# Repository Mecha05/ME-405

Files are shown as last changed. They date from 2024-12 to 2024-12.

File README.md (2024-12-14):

# ME-405
ME-405 Romi Portfolio

## Required materials:
1) Romi chasis of your desired color
2) Romi Drive and caster wheels
3) BNO055 IMU Breakout Board
4) Modified shoe of Brian
5) Nucleo L476RG
6) M2.5 x 8mm Standoff
7) M2.5 x 10mm Standoff
8) M2.5 x 30mm Standoff
9) M2.5 x 6mm Socket Head Cap Screw
10) M2.5 x 8mm Socket Head Cap Screw
11) M2.5 x 10mm Socket Head Cap Screw
12) M2.5 Nylon Lock Nuts
13) M2.5 Nylon Washers
14) Custom Romi to shoe adapter
15) Gearmotor and Encoder assembly
17) Motor driver and PDP for Romi
18) 8-channel QTRX sensor array
19) Bumper Switch Assembley (Right, Left, or both)
20) Assorted tools
21) Attached .txt files
22) Female to Felmale wires
23) Optional HC-05 Bluetooth modules

## **Getting Started:**
To get started follow the set-up instructions provided with the Romi chassis and on the Romi webpage to secure and attach the Motor driver and PDP for Romi, Gearmotor and Encoder assembly, and Romi Drive and caster wheels. The Gearmotor and Encoder assembly should plug directly into the PDP.

Romi should now look like this:


These highlighted section show necessary cable connections for power to the Nucleo, Motor control cables, and Encoder cables for communication between the PDP and our Nucleo. Example cables are shown below.



Following this step please attach the BNO055 IMU Breakout Board, in the specified location shown below. A different location may be needed depending on the quantity and location of bump sensors. Consider a custom mount on the aft part of Romi as the best solution.



Next step in to wire up the IMU, the necessary pins are power, ground, SDA, SCL, and RST. An example Cable set up is provided below:


Wiring the 8-channel QTRX sensor array comes next, I reccomend creating your cables using a 7x1 joined female end to 7 free ends to enable a solid connection on the array board while giving freedom to use any desired pins on the Nucleo. A pin our of the array board are given below.


To install the 8-channel QTRX sensor array, first fish the wire through the highlighted holes on the bottome of the Romi, shown belown, then place the board in the left over gap. You will need to secure the board, however be aware of blocking sensors or potential shorts. I reccomend taping the 7x1 joined adaptor to the standoffs for the nucleo, but do what every feels most secure.



This is what the bottom of Romi should look like after the instalation.


The final step in Romi assebly before wiring is the bump sensors. You are welcome to choose as many or as few as you would like. For our project we chose the Right assembly only. This was doen to avoid having to relocate the IMU. You will need a 4x1 cable and I reccomend having one end of this cable be 1x1s for port avalibility. The attached system should look like this (note this is with both installed)



## Wiring Set-Up:
Next step is the most critical to ensure that Romi opperates as intended. Below is the wiring diagram that we used for our project. If different ports are needed please reflect those changes in the code to ensure proper function.



> [!WARNING]
> Make sure to verify all ports, esspecially ground and power, before turning the system on. If not possible damage could occur to the components or sensors.

## Code Set-Up:
After verifying that your physcial pins match those specified in the code, load all of the attached .txt files into your python 3 program of choosing and save the file to the Romi as a .py file. Make sure that the .py file names match those verbatum of those of the .txt files, otherwise erros may occur.

The overall structure of the code to run the Romi around the track involves three states: Left Wheel, Right Wheel, and Velocity Control. The Left Wheel tasks runs the left motor and encoder of the Romi and controls the duty cycle based on a reference velocity specified from the velocity control task and a measured velocity from the left encoder. The Right Wheel tasks similarly runs the right motor and encoder of the Romi, controlling the duty cycle based on the reference velocity and the measured velocity from the left encoder. The Velocity control taks is the larger task, which controlls the overall behavior of the Romi. The velocity control task reads reads the line sensor data, calculates a weighted sum, and specifies a yaw rate based on the value of the weighted sum. Our control structure is a cascaded control structure with the left and right wheel motor controllers on the inner loop in the Left Wheel and Right Wheel tasks. The outer loop of our control system is contained within the velocity control task and it involves a longitudinal velocity controller and a yaw rate controller, which feed reference wheel velocities to the other two controllers. All the shares variables, motor objects, and controller must be defined correctly within all of the states to ensure good communication. Thec scheduler included in the cotask and task_share runs the tasks on time at a period of 6 miliseconds for the Left and Right Wheel Encoders and 8 ms for the velocity control task.

## Task Diagram

Term Project Task Diagram

The task diagram shows the interaction between the three different tasks. The task diagram shows that the left and right wheel tasks have a higher priority and shorter period than the velocity control task. The left and right wheel reference velocities are shared from the velocity control task, while the measured left and right wheel measured velocities are shared from the left and right wheel tasks respectively to the velocity control task. These velocities allow the controllers for each motor to control the motor speed to match the reference velocity calculated from the yaw rate and linear velocity controllers in the velocity task. Additionally, these share variables allow the yaw rate and linear velocity tasks to update based on the measured velocity from the left and right wheel tasks. The calibration flag, bump flag, and end flag variables are shared from the velocity control task to signal when the IMU has calibrated on startup, when the bump sensors are triggered, and when the Romi has reached the end of the track.

## Left Wheel Task

Left Wheel FSM

The Left Wheel Task Finite State Machine displays the three states within the Left Wheel task. State 0 is simply a setup state that runs only until the calibration flag reads true once the IMU has been calibrated in the Velocity Control task. State 1 is the state where the control of the motor occurs. State 1 updates the left encoder and calculates the measured velocity of the left wheel. State 1 takes in the shares variable, including the reference velocity of the left wheel from the Velocity Control task, which is fed into the left wheel PI controller. The left wheel controller will return a duty cycle for the motor to keep the measured velocity of the wheel at the reference velocity. Finally, state 1 also puts the velocity of the left wheel into the shares variable to be used in the Velocity Control task. State 2 is used to avoid the wall and return to the start once the bump flag or end flag is true, which has been harcoded within the Velocity Control task, meaning the left wheel task is in an idle state until the bump flag and end flag are false.

## Right Wheel Task

Right Wheel FSM

Similar to the Left Wheel Task, the Right Wheel Task Finite State Macine shows the three states within the Right Wheel task. State 0 runs and sets up the motor until the calibration flag reads true after the IMU has been calibrated in the Velocity Control Task. State 1 controls the right motor by updating the right aencoder and calculates the measured velocity. It also takes in the reference velocity of the right wheel from the Velocity control task, which is used in the right wheel PI controller. The PI controller returns a duty cycle to update the motor and keep the measured velocity of the right wheel at the reference velocity. State 2 is used to avoid the wall and return to the start once the bump flag or end flag is true, which has been haroded within the Velocity Control task, measning the left wheel task is in an idle state until the bump flag and end flag are flase.

## Velocity Control Task

Velocity Control FSM

The Velocity Control Task Finite State Machine shows the 4 states that are within the Velocity Control task. State 0 is a velocity setup task that initlizes the important objects, such as the line sensors, and calirates the IMU. Once the IMU is calibrated, the task will transition to state 1 and it will signal to the Left and Right Wheel Tasks that they must transition to state 1 as well. State 1 is where the majority of the control stucture is taking place. The state reads each of the line sensors, normalizes the reading, and calculates the weighted sum of the line sensor readings. Based on the value of the weighted sum, we update the yaw rate to control the behavior of the motor. If the absolute value of the weighted sum is small drive the motor straight when it is reading equal amounts of black and white on each side of the line sensor array. If the absolute value of the weighted sum is very large, the linear velocity of the Romi robot is decreased for the sharp curves to increase accuracy of reading the tight radii. If it has been less than about 2 seconds since the last sharp turn reading from the line sensor array, the Romi will continue to go slow. To ensure that the initial line of the starting box does not affect the robot, a condition has been included that will cause the Romi to continue straight if it reads 3 or more of the sensors over a black line in about 5 seconds after the Romi starts moving. The same logic is implemented to ignore when 5 or more of the sensors read as all black so that the Romi continues along the course track even with large vertical black lines in the path. However, if the bump flag has been triggered and the Romi reads 4 or more line sensors that read black, the Romi has reached the final box, which will cause it to reach state 3. Triggering the bump sensors will initiate the transition to state 2. With the yaw rate determined from the readings of the line sensors, state 1 of the Velocity Control task also inputs the reference linear velocity and yaw rate into the proporitonal controllers to keep the linear velocity and yaw rate similar to the reference values. These values of the linear velocity and yaw rate are then decoupled using our decoupling matrix, and are used to calculate the reference left and right wheel velocities for the Left and Right WHeel Task. Finally, state 1 puts the reference left and right wheel velocities into the shares variable to be shared with the other tasks.

State 2 occurs after one of the bump sensors has been triggered, and it causes the Romi to move backwards, then turn left, then move forwards, then turns right and moves forward for a certain amount of time. The duty cycle of the motors are set and tuned so that the Romi will avoid the wall and re-establish its position reading the line sensors. Once this sequence is complete, the variables are reset and the state transitions back to 1. State 3 occurs after the Romi has reached the final box and has read more than 4 black sensors at once, signifying an all black line. Once this occurs, state 3 causes the robot to continue forward for a small amount of time before turning around. The Romi knows when to start turning based on time, and it will stop turning once the current heading is within 0.5 degrees of the initial heading. The Romi will then briefly pause before driving forward to return to the starting box, completing the course. Once the Romi has returned to the start box, the motors are disabled and the program is complete.

The following section explains the function of each code python file within the repository.
## main
The main file contains the three tasks and runs the overall code, using all the other files and classes. This is the file that will control the Romi robot to complete the course.

## linesensor
The linesensor file contains the class to read the data from the linesensor and normalize the data by determining if the reading corresponds to a black or white reading and outputs a 0 or 1.

## centroid
The centroid file returns a weighted sum value which the main file uses to determine the desired yaw rate of the Romi.

## mot_romi
The mot_romi file contains the class to run the Romi motors and set the duty cycle of each motor object. This file is used to spin the motors based on our desired duty cycle.

## encoder_romi
The encoder_romi file contains the class to read the encoder of each wheel. The class contains method to update the encoders as well as return the position and delta values, which can be used to determine the velocity of the each wheel. The class also contains a method to zero the encoder object.

## closedloopleft
The closedloopleft file contains the PI controller to control the left motor. The class has a Kp and Ki value, and it returns a duty cycle based on the error between the measured and reference velocity for the left wheel.

## closedloopright
The closedloopright file contains the PI controller to control the left motor. The class has a Kp and Ki value, and it returns a duty cycle based on the error between the measured and reference velocity for the right wheel.

## linvelloop
The linvelloop file contains the Proportional controller to control the linear velocity of the Romi based on a specified reference velocity and the measured forward velocity of the Romi calculated from the encoders.

## yawrateloop
The yawrateloop file contains the Proportional controller to control the yaw rate based on the specified reference yaw rate based on the line sensor data from the velocity control task and the measured yaw rate from the IMU.

## BNO055
The BNO055 file contains the class for the functionality of the IMU. The file contains the class with methods to set the mode of the IMU, read and set calibration data, read the euler angles, heading, angular velocity, and yaw rate of the Romi robot.

## task_share
The task_share class is a class that allows share and queue variables to be created and share the data between the left wheel, right wheel, and velocity control tasks.

## cotask
The cotask file contains the class and the methods to run the scheduler, which runs the tasks based on the specified period and priority of each task specified by the user.

## Optional Attachments
In the attached files there is a .STL file that contains an object for a optional mount. This mount has mounting holes for both a single bump sensor and the 8-channel QTRX sensor array. However due to printing challengs we did not implement this feature into our design. However given more time this mout would be a very benifical thing to have. Locating the  8-channel QTRX sensor array out infront of the robot plus closer to the ground woul dhelp with smoother robot movements and clearer line tracking. Additionly by putting the bump sensor our from you eliminate the risk of not contacking the box, reduces the price of ordering both bump sensor assemblies, and the IMU does not need to be relocated.

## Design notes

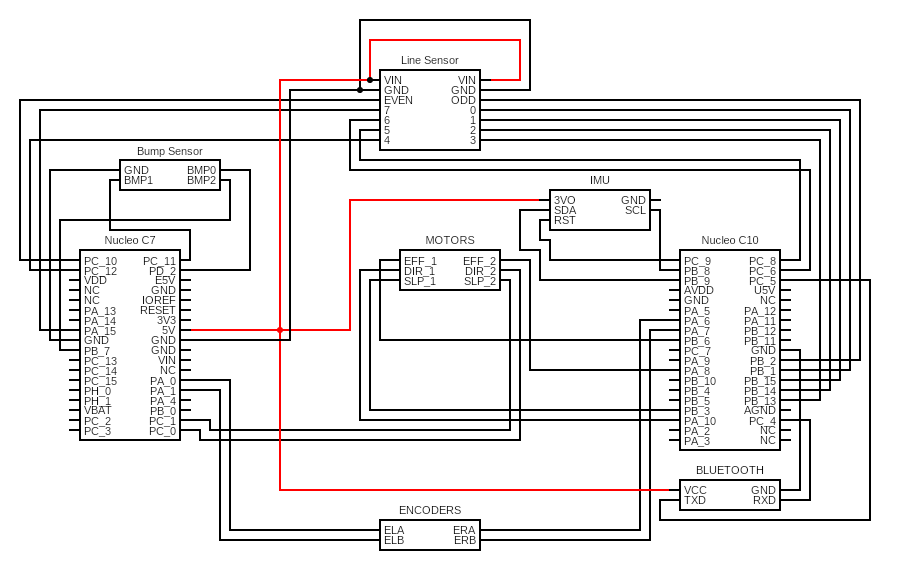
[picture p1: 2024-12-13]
circuit.png

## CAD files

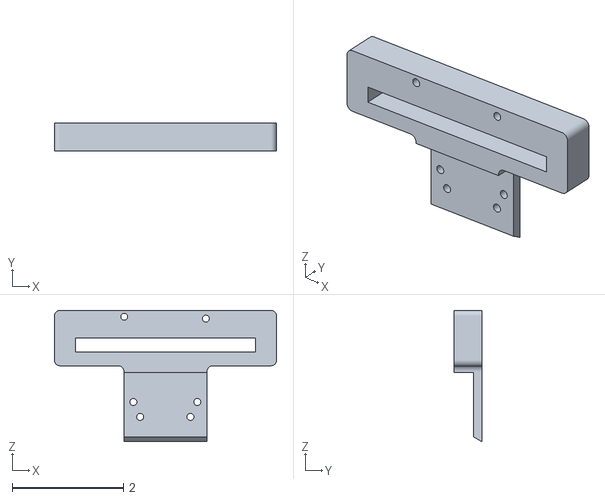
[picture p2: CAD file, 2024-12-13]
Sensor Adaptor.STL
4.00 x 0.5 x 2.37

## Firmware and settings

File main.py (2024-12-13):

'''!@file                          main.py
    @brief                         The main program to drive Romi in a circle
    @details                       A main file that uses 3 tasks to drive Romi around a
                                   track using line sensors, bump sensors, IMU sensors, 
                                   Romi motors and encoders, and closed loop feedback. A 
                                   user specifies the linear velocity and the yaw rate based
                                   on the weighted sum from the line sensor data, and the Romi 
                                   will used datafrom the IMU to determine the yaw rate and the 
                                   encoders to determine the linear velocity to drive 
                                   around the specified track.
    @author                        Cole Lunde and Nate Hempstead
    @date                          December 13, 2024
'''

import cotask
import task_share
from pyb import Pin, Timer, I2C, UART, repl_uart
from encoder_romi import Encoder_romi
from time import ticks_ms, ticks_diff, sleep
from mot_romi import MotorDriver
import gc
from array import array
from closedloopright import ClosedLoopRight
from closedloopleft import ClosedLoopLeft
from linvelloop import LinVelLoop
from yawrateloop import YawRateLoop
from BNO055 import BNO055
from linesensor import LineSensor
from centroid import Centroid

def wheel_L(shares):
    '''!@brief                     A task to run and control the left wheel of Romi
        @details                   A task with two states that initializes the left motor and 
                                   encoder, and runs the left motor at a specified duty cycle. 
                                   The duty cycle is determined using a PI controller to control
                                   the left motor.
        @param shares              A tuple of multiple shares to share data from and with the task
    '''
    # set state to 0
    state = 0
    
    # Run FSM
    while True:
        # State 0 - Motor Setup
        if state == 0:

            # Enable the motor
            mot_L.enable()
            mot_L.set_duty(0)

            # Zero encoder for left wheel
            enc_L.zero()
            # Set start time as current time
            old_time = ticks_ms()
            # Create controller object for left wheel motor
            cont_L = ClosedLoopLeft()
            # Define variables from shares
            my_velocityL_ref, my_velocityL_meas, my_calib_flag, my_bump_flag, my_end_flag = shares
            L = 0
            
            # Set state to 1 only if IMU is calibrated
            if my_calib_flag.get() == 1:
                state = 1    
            yield state
    
        # State 1 - Update Encoder and Motor Control
        elif state == 1:
            # Update current time
            now = ticks_ms() 
            # Update the encoder and velocity measured
            enc_L.update()
            velL = enc_L.get_delta()/(ticks_diff(now,old_time))
            # Correct the measurement to rad/s  units
            velL = velL*2*3.1415*1000/1440
            # Set old time to current time
            old_time = now
            
            # Get desired velocity from shares
            omega_L = my_velocityL_ref.get()
            
            # Set Duty Cycle based on desired velocity and measured velocity
            L = cont_L.duty(omega_L, velL)
            mot_L.set_duty(L)
            
            # Put measured velocity into the shares variable
            my_velocityL_meas.put(velL)
            
            if (my_bump_flag.get() ==1):
                state=2
            if (my_end_flag.get()==1):
                state = 2
                    
            yield state
        elif state==2:
            #print('Left state 2')
            if (my_bump_flag.get() ==0 and my_end_flag.get() == 0):
                state=1
            yield state
        
        else: 
            raise ValueError('Invalid state')
            
def wheel_R(shares):
    '''!@brief                     A task to run and control the right wheel of Romi
        @details                   A task with two states that initializes the right motor and 
                                   encoder, and runs the right motor at a specified duty cycle. 
                                   The duty cycle is determined using a PI controller to control
                                   the right motor.
        @param shares              A tuple of multiple shares to share data from and with the task
    '''
    # Set state to 0
    state = 0
    
    # Run FSM
    while True:
        # State 0 - Motor Setup
        if state == 0:
            
            #Enable the motor and set duty cycle to 0
            mot_R.enable()
            mot_R.set_duty(0)

            # Zero Encoder R
            enc_R.zero()
            
            # Set old time to now
            old_time = ticks_ms()
            # Create controller object for right wheel motor
            cont_R = ClosedLoopRight()
            # Define variables from shares
            my_velocityR_ref, my_velocityR_meas, my_calib_flag, my_bump_flag, my_end_flag = shares
            
            # Set state to 1 if IMU is calibrated
            if my_calib_flag.get() == 1:
                state = 1
   
            yield state
    
        # State 1 - Update Encoder and Motor Control
        elif state == 1:
            # Update Current time
            now = ticks_ms()
            # Update the encoder and velocity measured
            enc_R.update()
            velR = enc_R.get_delta()/(ticks_diff(now,old_time))
            # Correct the measurement to rad/s units
            velR = velR*2*3.1415*1000/1440
            # Set old time to current time
            old_time = now
            
            # Get reference velocity from shares
            omega_R = my_velocityR_ref.get()

            # Set Duty Cycle based on desired velocity and measured velocity
            L = cont_R.duty(omega_R, velR)
            mot_R.set_duty(L)
            
            # Put measured velocity into shares variable
            my_velocityR_meas.put(velR)

            if (my_bump_flag.get()==1):
                state = 2
            if (my_end_flag.get()==1):
                state = 2
                
            yield state
        elif state == 2:
            #print('Right state 2')
            if (my_bump_flag.get() ==0 and my_end_flag.get() == 0):
                state=1
            yield state
        else: 
            raise ValueError('Invalid state')
            
def VelControl(shares):
    '''!@brief                     A task to run and control the linear velocity and yaw rate of Romi
        @details                   A task with four states that initializes the IMU and calibrates it.
                                   The task takes in data from the LineSensor and Centroid class that
                                   creates a weighted sum, which determines the specified yaw rate.
                                   The task specifies the linear velocity and uses the yaw rate
                                   from the centroid class before creating objects for linear 
                                   velocity and yaw rate controllers. The task uses these controllers
                                   and the data from the encoders to control the yaw rate and linear 
                                   velocity of Romi. The task calculates new reference velocities
                                   for the left and right motor and sends these values to the wheel_L
                                   and wheel_R tasks.The task monitors the bump sensors and runs the 
                                   Romi around the box if the bump sensors are triggered. The task also
                                   returns the Romi to the start of the track.
        @param shares              A tuple of multiple shares to share data from and with the task
    '''
    # Define state 0
    state = 0
    
    # Run FSM
    while True:
        # State 0 - Setup
        if state == 0:
            # Define reference variables from shares
            our_velL_ref, our_velL_meas, our_velR_ref, our_velR_meas, our_calib_flag, our_bump_flag, our_end_flag = shares
            
            # Define trackwidth
            w = 0.141
            # Define wheel radius
            r_w = 0.035
            # Define Linear Velocity
            lin_vel = 0.2
            
            # Define calibration flag variable
            calib_flag = 0
            # Define bump flag variable
            bump_flag = 0
            
            all_ones = True
            # Initialize Sharp time
            sharp_time = 0
            
            turn_done_flag = 0

            # Define sensor pins
            sensor_0_pin = Pin(Pin.cpu.A15, mode=Pin.OUT_PP)
            sensor_1_pin = Pin(Pin.cpu.C6, mode=Pin.OUT_PP)
            sensor_2_pin = Pin(Pin.cpu.C8, mode=Pin.OUT_PP)
            sensor_3_pin = Pin(Pin.cpu.C12, mode=Pin.OUT_PP)
            sensor_4_pin = Pin(Pin.cpu.B13, mode=Pin.OUT_PP)
            sensor_5_pin = Pin(Pin.cpu.B14, mode=Pin.OUT_PP)
            sensor_6_pin = Pin(Pin.cpu.B15, mode=Pin.OUT_PP)
            sensor_7_pin = Pin(Pin.cpu.B1, mode=Pin.OUT_PP)
            
            # Define Control Odd and Even Pins
            ctrl_odd_pin = Pin(Pin.cpu.B2, mode=Pin.OUT_PP)
            ctrl_even_pin = Pin(Pin.cpu.C10, mode=Pin.OUT_PP)
            
            # Set the Pins high
            ctrl_odd_pin.high()
            ctrl_even_pin.high()

            # Define Sensor Objects
            sensor_0 = LineSensor(sensor_0_pin)
            sensor_1 = LineSensor(sensor_1_pin)
            sensor_2 = LineSensor(sensor_2_pin)
            sensor_3 = LineSensor(sensor_3_pin)
            sensor_4 = LineSensor(sensor_4_pin)
            sensor_5 = LineSensor(sensor_5_pin)
            sensor_6 = LineSensor(sensor_6_pin)
            sensor_7 = LineSensor(sensor_7_pin)
            
            # Create a sensor readings array
            readings = array('H', 8*[10])
            
            # Initialize Bump Sensor Pins as inputs
            bump_sensor_0 = Pin(Pin.cpu.D2, mode = Pin.IN, pull = Pin.PULL_UP)
            bump_sensor_1 = Pin(Pin.cpu.C11, mode = Pin.IN, pull = Pin.PULL_UP)
            bump_sensor_2 = Pin(Pin.cpu.B7, mode = Pin.IN, pull = Pin.PULL_UP)
            
            
            tleft_time = None
            current_time = None
            
            # Initialize controller objects for linear velocity and yaw rate
            lin_cont = LinVelLoop()
            yaw_cont = YawRateLoop()
            
            # Initialize IMU i2c object
            i2c = I2C(1, I2C.CONTROLLER, baudrate=100000)
            imu = BNO055(i2c, Pin.cpu.B9, Pin.cpu.B8, Pin.cpu.C9)
            imu.set_mode(0x0C)  # NDOF mode
            
            # Read Calibration Status of the IMU and display it
            sys_calib_status, gyr_calib_status, acc_calib_status, mag_calib_status = imu.get_calib_status()
            print(f"{sys_calib_status}, {gyr_calib_status}, {acc_calib_status}, {mag_calib_status}")
            
            # If IMU is fully calibrated, set calib_flag to 1 to signal that it is calibrated 
            if sys_calib_status == 3 and gyr_calib_status == 3 and acc_calib_status == 3 and mag_calib_status == 3:
                calib_flag = 1
                print("Calibration Complete")
                our_calib_flag.put(calib_flag)
                
            our_calib_flag.put(calib_flag)   
            
            # Set state to 1
            if calib_flag == 1:
                sleep(10)
                init_heading = imu.read_heading()
                print(f"{init_heading}")
                done_time = ticks_ms()
                state = 1
            
            yield state
            
            # State 1 - Velocity Control
        elif state == 1:
            
            # Get actual left and right wheel velocities
            omega_L_act = our_velL_meas.get()
            omega_R_act = our_velR_meas.get()
                    
            if (bump_sensor_0.value() == 0 or bump_sensor_1.value() == 0 or bump_sensor_2.value() == 0):
                print('bumped')
                back_time = ticks_ms()
                tright_time = None
                tleft_time = None
                our_bump_flag.put(1)
                bump_flag = 1
                state = 2
            
            # Read all the line sensors
            sensor_7_reading = sensor_0.read_sensor()
            sensor_6_reading = sensor_1.read_sensor()
            sensor_5_reading = sensor_2.read_sensor()
            sensor_4_reading = sensor_3.read_sensor()
            sensor_3_reading = sensor_4.read_sensor()
            sensor_2_reading = sensor_5.read_sensor()
            sensor_1_reading = sensor_6.read_sensor()
            sensor_0_reading = sensor_7.read_sensor()
            
            # Normalize line sensor values
            sensor_0_nreading = sensor_0.normalize_reading(sensor_0_reading)
            sensor_1_nreading = sensor_1.normalize_reading(sensor_1_reading)
            sensor_2_nreading = sensor_2.normalize_reading(sensor_2_reading)
            sensor_3_nreading = sensor_3.normalize_reading(sensor_3_reading)
            sensor_4_nreading = sensor_4.normalize_reading(sensor_4_reading)
            sensor_5_nreading = sensor_5.normalize_reading(sensor_5_reading)
            sensor_6_nreading = sensor_6.normalize_reading(sensor_6_reading)
            sensor_7_nreading = sensor_7.normalize_reading(sensor_7_reading)
            
            # Add all line sensor values into a readings array
            readings[0] = sensor_0_nreading
            readings[1] = sensor_1_nreading
            readings[2] = sensor_2_nreading
            readings[3] = sensor_3_nreading
            readings[4] = sensor_4_nreading
            readings[5] = sensor_5_nreading
            readings[6] = sensor_6_nreading
            readings[7] = sensor_7_nreading
            
            #print(f"{readings}")
            
            # Determine the weighted sum of the readings
            sensor_reading = Centroid(readings)
            reading = sensor_reading.weighted_sum()
            #print(reading)
            
            if -1 <= reading <= 1:
                yaw_rate = 0
            elif -11 <= reading < -1:
                yaw_rate = -3
            elif reading < -11:
                yaw_rate = -5
                sharp_time = ticks_ms()
            elif 1 < reading <= 11:
                yaw_rate = 3
            else:  
                yaw_rate = 5
                sharp_time = ticks_ms()
                
            # Get current time
            current_time = ticks_ms()
            
            # If it has been less than 1.5 seconds since a +/- 12 reading
            if ticks_diff(current_time, sharp_time) < 2000:
                # Set linear velocity to slower rate
                lin_vel = 0.065
            else:
                # Set linear velocity to normal rate
                lin_vel = 0.2
        
        
            # Reading sum variable initialized
            reading_sum = 0
            all_ones = False
            
            print(ticks_diff(current_time, done_time))
            if bump_flag == 1 and ticks_diff(current_time,done_time) >= 12000:
                for value in readings: 
                    reading_sum += value
                    if reading_sum >= 4:
                        all_ones = True
                if all_ones == True:
                    all_ones_time= ticks_ms()
                    our_end_flag.put(1)
                    state = 3
            elif ticks_diff(current_time,done_time) <= 12000:
                  for value in readings:
                      reading_sum += value
                      if reading_sum >= 3:
                          all_ones = True
                  if all_ones == True:
                      yaw_rate = 0  
                      lin_vel = 0.2
            else:
                for value in readings:
                    reading_sum += value
                    if reading_sum >= 5:
                        all_ones = True
                if all_ones == True:
                    yaw_rate = 0  
                    lin_vel = 0.25
                    
            # Calculate measured linear velocity
            lin_vel_meas = (omega_L_act + omega_R_act)*(r_w/2)
            
            # Get desired linear velocity from controller
            lin_vel_ref = lin_cont.set_vel(lin_vel, lin_vel_meas)
           # print(f"{lin_vel}, {lin_vel_ref}, {lin_vel_meas}")
            
            # Read IMU to get angular velocity
            IMU_yaw_rate = imu.read_yaw_rate()
            # Convert from degrees to rad
            yaw_rate_meas = IMU_yaw_rate * 3.1415/180
           
            # Calculate measured yaw rate
            yaw_rate_meas = (omega_R_act-omega_L_act)*(r_w/w)
            # Get desired yaw rate from controller
            yaw_rate_ref = yaw_cont.set_yaw(yaw_rate, yaw_rate_meas)
            #print (yaw_rate_ref)
            
            # Calculate desired left and right motor velocities
            omega_L_ref = ((lin_vel_ref)/r_w) - (w/(2*r_w))*yaw_rate_ref
            omega_R_ref = ((lin_vel_ref)/r_w) + (w/(2*r_w))*yaw_rate_ref
            
            # Put desired left and right motor velocities in shares
            our_velL_ref.put(omega_L_ref)
            our_velR_ref.put(omega_R_ref)
            
            curr_heading = imu.read_heading()
            print(f"{curr_heading}, {init_heading}")
            
            yield state
            
        # State 2 - Bumped
        elif state == 2:
            now_time = ticks_ms()
            # First: Handle "back" movement
            if ticks_diff(now_time, back_time) <= 800:
                print('back')
                #print(f"{lin_vel}, {lin_vel_ref}, {lin_vel_meas}")
                mot_L.set_duty(-30)
                mot_R.set_duty(-30)                
                tright_time = None
                tleft_time = None
            else:
                if tright_time is None: # Set tright_time only once
                    tright_time = ticks_ms()  # Record the start time of "right" state
                elif ticks_diff(now_time, tright_time) <= 550:
                    # Continue "right" movement
                    print('Turn R')
                    mot_L.enable()
                    mot_R.disable()
                    mot_L.set_duty(30)
                elif ticks_diff(now_time, tright_time) <= 1200:
                    # Forward movement
                    print('frwd')
                    mot_R.enable()
                    mot_L.set_duty(30)
                    mot_R.set_duty(30)
                else:
                    if tleft_time is None: # Set tright_time only once
                        tleft_time = ticks_ms()  # Record the start time of "right" state
                    elif ticks_diff(now_time, tleft_time) <= 460:
                        # Continue "right" movement
                        print('Turn L')
                        mot_R.enable()
                        mot_L.disable()
                        mot_R.set_duty(30)
                    elif ticks_diff(now_time, tleft_time) <= 2500:
                        # Forward movement
                        print('frwd')
                        mot_L.enable()
                        mot_L.set_duty(27)
                        mot_R.set_duty(30)
                    else:
                        # Return to state 1
                        print('transition to state 1')
                        # Ensure tright_time and tleft_time are reset here
                        done_time = ticks_ms()
                        tright_time = None
                        tleft_time = None
                        state = 1
                        # Reset bump flag share variable
                        our_bump_flag.put(0)
            
            yield state
            
        # State 3 - Return to Start    
        elif state == 3:
            # Get the current heading from the imu
            curr_heading = imu.read_heading()
            #print(f"{curr_heading}, {init_heading}")
            # Record the time when all black is read
            all_ones_now = ticks_ms()
            # Go forward for 600 ms
            if ticks_diff(all_ones_now, all_ones_time) <= 600:
                print('forward')
                mot_L.set_duty(20)
                mot_R.set_duty(20)
            # Turn around until the heading is accurate
            elif abs(curr_heading - init_heading) >= .5 and turn_done_flag == 0:
                print('turn')
                mot_L.set_duty(-10)
                mot_R.set_duty(10)
                turn_time = ticks_ms()
            # Pause for  500 ms
                print(f"{curr_heading}, {init_heading}")
            elif ticks_diff(all_ones_now, turn_time) <= 500:
                print('stopped')
                turn_done_flag = 1
                mot_L.set_duty(0)
                mot_R.set_duty(0)
            # Go Forward for the next 3600 ms
            elif ticks_diff(all_ones_now, turn_time) <= 2050:
                #IF NOT WORK PUT BACK TO <= 4100, L=34.5, R=30
                #print('forward to start')
                mot_L.set_duty(64.5)
                mot_R.set_duty(60)
            # Disable the motors as the Track has been completed
            else:
                #print('done')
                mot_L.disable()
                mot_R.disable()
            yield state
            
        else:
            raise ValueError('Invalid State')
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

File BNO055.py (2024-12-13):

'''!@file                          BNO055.py
    @brief                         A class to read from and write to the BNO055 IMU
    @details                       A class to initialize a BNO055 I2C IMU object with methods
                                   set_mode to set the mode of the imu, get calib_status to return
                                   the status of the IMU calibration, get_calib_coeffs to get the
                                   calibration coefficients of the object, set_calib_coefficients
                                   to set the calibration coefficients, read_euler to read the 
                                   heading roll and pitch data, read_heading to return only the 
                                   heading data, read_angular_velocity to return the gyroscope 
                                   data of heading rate, pitch rate, and yaw rate, and get_yaw_rate
                                   to get just the yaw rate data from the object.
    @author                        Cole Lunde and Nate Heampstead
    @date                          December 13, 2024
'''

from pyb import Pin, I2C
import time
import struct

class BNO055:
    def __init__(self, i2c, sda, scl, reset):
        '''!@brief                      Initializes objects of the BNO055 class.
            @details                    Takes in an i2c object, sda, scl, and reset pin and specifies the address,
                                        mode, and reset pin to high of the BNO055 object.
            @param i2c                  An i2c object previously created
            @param sda                  The pin object used for the sda
            @param scl                  The pin objectused for the scl
            @param reset                The pin object used for reset
        '''
        self.i2c=i2c
        self.addr = 0x28  # Default I2C address for BNO055
        self.mode = 0x00  # Default mode
        
        # Initialize the reset pin
        self.reset_pin = Pin(reset, Pin.OUT_PP)
        self.reset_pin.high()  # Ensure reset pin is high (active low)
        time.sleep(0.75)

    def set_mode(self, mode):
        '''!@brief                      Sets the mode of the BNO055 object.
            @details                    Takes in a mode value to write to the BNO055 object at the mode address
                                        of 0x3D.
            @param mode                 The desired mode to set the BNO055 to
        '''
        # Set the mode of the BNO055
        self.mode = mode
        self.i2c.mem_write(self.mode, self.addr, 0x3D)  # Register address for mode setting
        time.sleep(0.05)

    def get_calib_status(self):
        '''!@brief                      Gets the calibration status of the BNO055 IMU
            @details                    Gets the calibration status by reading the calibration status byte on
                                        the BNO055 IMU. Unpacks the byte and assigns the two bits to the system,
                                        gyroscope, accelermoeter, and the magnetometer.
            @return                     The four calibration status as a number 0-3
        '''
        # Get the calibration status from the IMU
        calib_stat = bytearray([0 for n in range(1)])
        calib_stat = self.i2c.mem_read(calib_stat, self.addr, 0x35)
        # Unpack the calibration status and assign bytes to the sys, gyr, acc, and mag
        calib_byte, = struct.unpack('<B', calib_stat)
        sys_calib = (calib_byte >> 6) & 0x03  
        gyr_calib = (calib_byte >> 4) & 0x03  
        acc_calib = (calib_byte >> 2) & 0x03  
        mag_calib = calib_byte & 0x03         
        return sys_calib, gyr_calib, acc_calib, mag_calib
        

    def get_calib_coeffs(self):
        '''!@brief                      Gets the calibration coefficients of the BNO055 IMU
            @details                    Gets the calibration coefficients by reading the calibration coefficients
                                        bytes on the BNO055 IMU. Unpacks the bytes and assigns the coefficients to the
                                        gyroscope, accelermoeter, and the magnetometer.
            @return                     The  calibration coefficients as a signed int
        '''
        calib_coeffs = bytearray([0 for n in range(22)])
        self.i2c.mem_read(calib_coeffs, self.addr, 0x55)
        acc_offset_x, acc_offset_y, acc_offset_z = struct.unpack('<hhh', calib_coeffs[0:6])
        mag_offset_x, mag_offset_y, mag_offset_z = struct.unpack('<hhh', calib_coeffs[6:12])
        gyr_offset_x, gyr_offset_y, gyr_offset_z = struct.unpack('<hhh', calib_coeffs[12:18])
        acc_radius, mag_radius = struct. unpack('<hh', calib_coeffs[18:22])
        return (acc_offset_x, acc_offset_y, acc_offset_z,
            mag_offset_x, mag_offset_y, mag_offset_z,
            gyr_offset_x, gyr_offset_y, gyr_offset_z,
            acc_radius, mag_radius)

    def set_calib_coeffs(self, calib_data):
        '''!@brief                      Sets the calibration coefficients of the BNO055 IMU
            @details                    Sets the calibration coefficients by writing to the calibration coefficients
                                        bytes on the BNO055 IMU. 
            @param calib_data           The calibration coefficients data to write to the BNO055 IMU
        '''
        self.i2c.mem_write(calib_data, self.addr, 0x55)
        time.sleep(0.05)

    def read_euler(self):
        '''!@brief                      Gets the euler angles data of the BNO055 IMU
            @details                    Gets the euler angles data by reading the 6 bytes with the euler data 
                                        on the BNO055 IMU. Unpacks the bytes and assigns the coefficients to 
                                        heading, roll, and pitch.
            @return                     The heading, roll, and pitch in degrees.
        '''
        euler_data = bytearray([0 for n in range(6)])
        self.i2c.mem_read(euler_data, self.addr, 0x1A)  # Start of Euler angles data
        heading, roll, pitch = struct.unpack('<hhh', euler_data)
        return heading/16.0, roll/16.0, pitch/16.0
    
    def read_heading(self):
        '''!@brief                      Gets the heading data of the BNO055 IMU
            @details                    Gets the heading data by reading the 2 bytes with the heading data 
                                        on the BNO055 IMU. Unpacks the bytes and assigns the coefficients to 
                                        heading.
            @return                     The heading in degrees.
        '''
        heading_data = bytearray([0 for n in range(2)])
        self.i2c.mem_read(heading_data, self.addr, 0x1A)
        heading, = struct.unpack('<h', heading_data)
        return heading/16.0
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

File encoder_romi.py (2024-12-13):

'''!@file                         encoder_romi.py
     @brief                       A driver for reading from Quadrature Encoders on the Romi
     @details                     A class that reads the encoder data from the encoders on the 
                                  Romi motors. The file includes only the Encoder_Romi class.
     @author                      Cole Lunde and Nate Hempstead
     @date                        December 13, 2024
'''
from pyb import Timer

class Encoder_romi:
    '''@brief                     Interface with qudrature econders
       @details                   The object is initialized, has an update method
                                  that updates all the necessary values, a get_position method
                                  that returns the position of the encoder, a get_delta method
                                  that reutrns the delta from the last call of update, a zero
                                  method that zeros the position of the encoder.
    '''
    
    def __init__(self, EN_tim, CH_A_Pin, CH_B_Pin):
        '''!@brief                 constructs an encoder object
            @details               The __init__ method creates the object assigning encoder timer object
                                  to the self variable, sets the pins of the encoder timer from the given
                                  arguments, and sets the counter as the counter of the encoder timer. It
                                  also sets the autoreload value and sets the position and old count to 0.
            @param EN_tim         A timer object to use for the encoder object
            @param CH_A_Pin       A pin object to be assigned to channel 1 of the encoder object
            @param CH_B_Pin       A pin object to be assigned to channel 2 of the encoder object
        '''
        # Assign timer and pins based on given arguments
        self.EN_tim = EN_tim
        self.EN1 = EN_tim.channel(1, pin=CH_A_Pin, mode=Timer.ENC_AB)
        self.EN2 = EN_tim.channel(2, pin=CH_B_Pin, mode=Timer.ENC_AB)
        self.EN_counter = EN_tim.counter()
        self.AR = 65535
        self.postion = 0
        self.count_old = 0
        
    def update(self):
        '''!@brief              Updates encoder position and delta
            @details            The update method gets the new count and calculates the delta from the new
                                and old count before resetting the old count to the new count. The method 
                                also updates delta properly if rollover has occurred in either direction.
                                It then adds the delta to the position to update the position.
        '''
        # Read the new count, calculate delta, and reset the old count
        self.count_new = self.EN_tim.counter()
        self.delta = self.count_new - self.count_old
        self.count_old = self.count_new
        # Update delta if rollover has occurred
        if self.delta > ((self.AR+1)/2):
            self.delta = self.delta - (self.AR+1)
        if self.delta < (-(self.AR+1)/2):
            self.delta = self.delta + (self.AR+1)
        self.position += self.delta
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
